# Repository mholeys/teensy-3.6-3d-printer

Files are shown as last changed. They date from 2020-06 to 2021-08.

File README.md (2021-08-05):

# Teensy 3.6 3D printer

KiCad board of my 3D printer

Uses a Teensy 3.6 - https://www.pjrc.com/store/teensy36.html
This requires most pins (including pins on the bottom of the teensy, as such I have left space for a row of wires to be soldered from the bottom of the teensy to the board.
This board was designed to replace a Anet A8 board so not all 3D printer features have been planned or taken into account.

Disclaimer:
- I am not a electrical engineer or certified in anyway for work with electronics, I am happy to take the risk myself but if you use this design you take all responsability, for any damage and you accept this.

Problems:
- After having the boards produced, I noticed that I have made a mistake with the holes for the custom boards such as the the rear pin breakout, and the TMC2130 driver holes. This has not been a problem for me as I have some smaller round hole pin headers, which fit perfectly, but you may have to redesign or modify this board in order to use something different.
- After using the board for a while, I have noticed I have also undersized the traces! (BAD, same problem as the original Anet A8 baord). This can be fixed by adding additional cabling between the GND input and the stepper motors, and importantly the transistors for the hot ends. This may make this board dangerous to use, and another reason not to use this board AS IS. 

Uses:
- https://github.com/XenGi/teensy_library
- https://github.com/XenGi/teensy.pretty

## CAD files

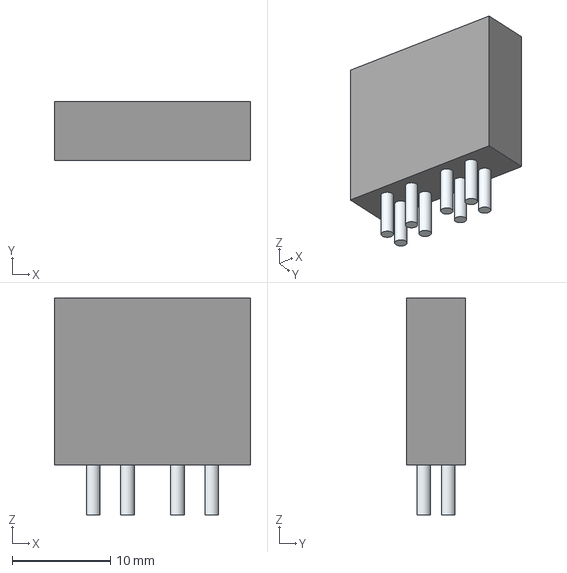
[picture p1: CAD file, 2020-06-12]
fuse/Pudenz-30a-PCB-ATO-Fuseholder.stp
20.0 x 6.00 x 22.1 mm
Leads x 9

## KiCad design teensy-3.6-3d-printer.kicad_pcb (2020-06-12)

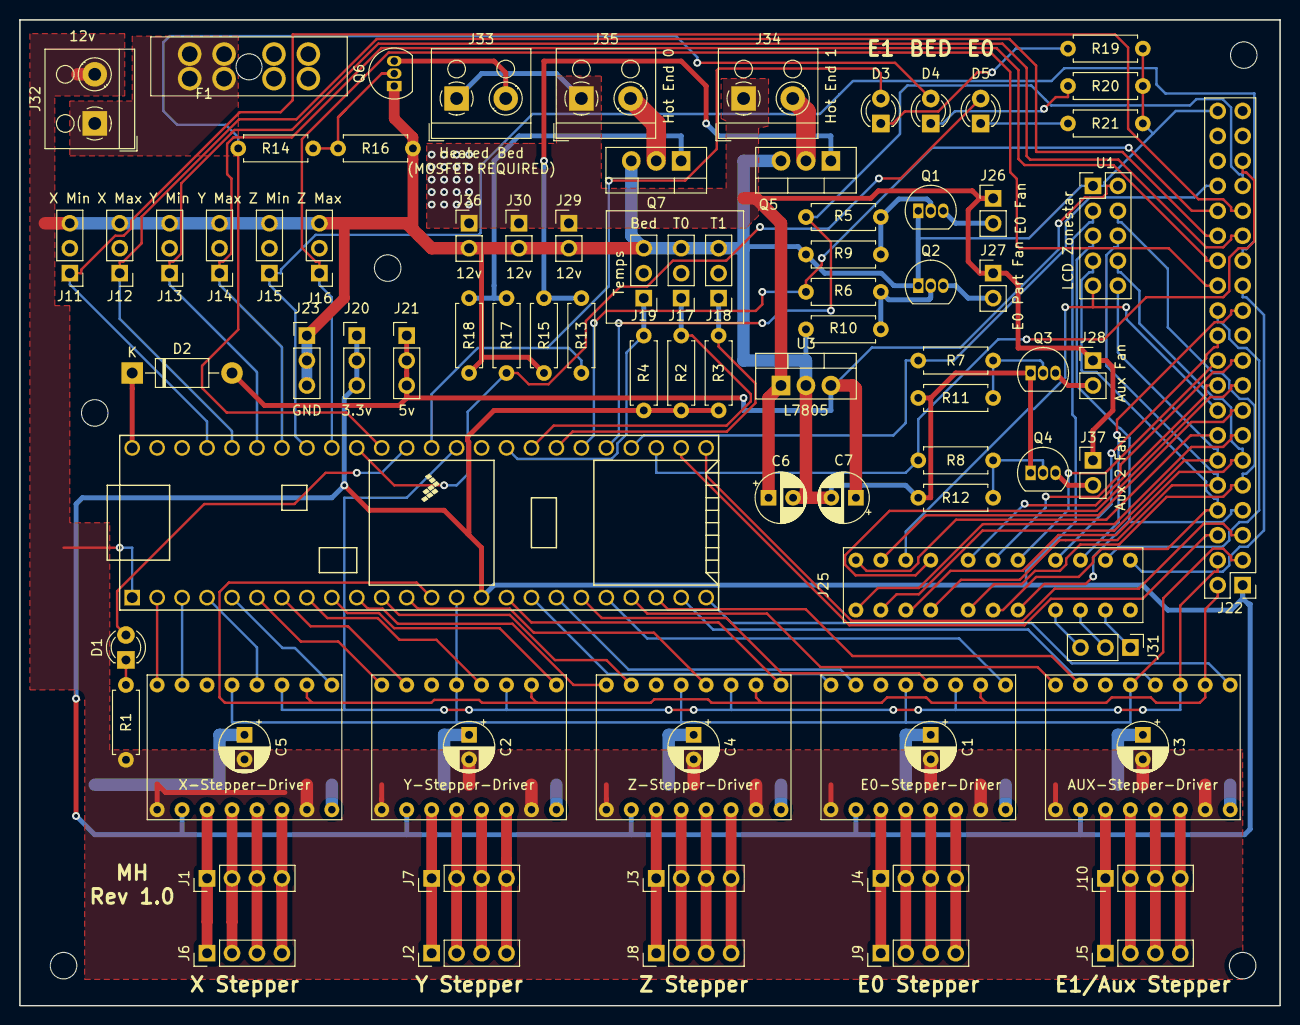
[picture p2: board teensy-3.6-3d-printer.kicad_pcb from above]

Board: 2 copper layers, 128.3 x 100.3 mm, 85 parts (0 on the bottom side), 107 nets.

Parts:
AUX-Stepper-Driver: TMC2130-Board; tmc2130-driver
C1, C2, C3, C4, C5: 100uf; CP_Radial_D5.0mm_P2.50mm
C6: 0.33uf; CP_Radial_D5.0mm_P2.50mm
C7: 0.1uf; CP_Radial_D5.0mm_P2.50mm
D1, D3, D4, D5: LED; LED_D3.0mm
D2: DIODE_SCHOTTKY_15V_1A; D_DO-41_SOD81_P10.16mm_Horizontal
E0-Stepper-Driver: TMC2130-Board; tmc2130-driver
F1: Fuse; Pudenz-30a-PCB-ATO-Fuseholder
J1, J6: X_STEPPER; PinHeader_1x04_P2.54mm_Vertical
J2, J7: Y_STEPPER; PinHeader_1x04_P2.54mm_Vertical
J3, J8: Z_STEPPER; PinHeader_1x04_P2.54mm_Vertical
J4, J9: E0_STEPPER; PinHeader_1x04_P2.54mm_Vertical
J5, J10: AUX_STEPPER; PinHeader_1x04_P2.54mm_Vertical
J11: X-Min-Limit; PinHeader_1x03_P2.54mm_Vertical
J12: X-Max-Limit; PinHeader_1x03_P2.54mm_Vertical
J13: Y-Min-Limit; PinHeader_1x03_P2.54mm_Vertical
J14: Y-Max-Limit; PinHeader_1x03_P2.54mm_Vertical
J15: Z-Min-Limit; PinHeader_1x03_P2.54mm_Vertical
J16: Z-Max-Limit; PinHeader_1x03_P2.54mm_Vertical
J17: Temp0; PinHeader_1x03_P2.54mm_Vertical
J18: Temp1; PinHeader_1x03_P2.54mm_Vertical
J19: Bed-Temp; PinHeader_1x03_P2.54mm_Vertical
J20: 3.3V; PinHeader_1x03_P2.54mm_Vertical
J21: 5V; PinHeader_1x03_P2.54mm_Vertical
J22: Conn_02x20_Counter_Clockwise; PinHeader_2x20_P2.54mm_Vertical
J23: GND; PinHeader_1x03_P2.54mm_Vertical
J25: teensy_back_pins; teensy-back
J26: Extruder 0 Fan; PinHeader_1x02_P2.54mm_Vertical
J27: Extruder 0 Part Fan; PinHeader_1x02_P2.54mm_Vertical
J28: Aux Fan; PinHeader_1x02_P2.54mm_Vertical
J29, J30, J36: 12V; PinHeader_1x02_P2.54mm_Vertical
J31: Debug; PinHeader_1x03_P2.54mm_Vertical
J32: Printer Power IN; TerminalBlock_RND_205-00001_1x02_P5.00mm_Horizontal
J33: Heated Bed; TerminalBlock_RND_205-00001_1x02_P5.00mm_Horizontal
J34: Hot End 1; TerminalBlock_RND_205-00001_1x02_P5.00mm_Horizontal
J35: Hot End 0; TerminalBlock_RND_205-00001_1x02_P5.00mm_Horizontal
J37: Aux 2 Fan; PinHeader_1x02_P2.54mm_Vertical
Q1, Q2, Q3, Q4, Q6: PN2222A; TO-92_Inline
Q5, Q7: IRLZ44N; TO-220-3_Vertical
R1, R14, R19, R20, R21: R; R_Axial_DIN0207_L6.3mm_D2.5mm_P7.62mm_Horizontal
R2, R3, R4: 4.7K; R_Axial_DIN0207_L6.3mm_D2.5mm_P7.62mm_Horizontal
R5, R6, R7, R8, R13, R17: 1K; R_Axial_DIN0207_L6.3mm_D2.5mm_P7.62mm_Horizontal
R9, R10, R11, R12, R15, R16, R18: 100K; R_Axial_DIN0207_L6.3mm_D2.5mm_P7.62mm_Horizontal
U1: Zonestar-LCD2004; PinHeader_2x05_P2.54mm_Vertical
U2: Teensy3.6; Teensy35_36
U3: L7805; TO-220-3_Vertical
X-Stepper-Driver: TMC2130-Board; tmc2130-driver
Y-Stepper-Driver: TMC2130-Board; tmc2130-driver
Z-Stepper-Driver: TMC2130-Board; tmc2130-driver

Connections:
+3V3: AUX-Stepper-Driver.3, E0-Stepper-Driver.3, J20.1, J20.2, J20.3, J22.1, R2.1, R3.1, R4.1, U1.3, U2.15, X-Stepper-Driver.3, Y-Stepper-Driver.3, Z-Stepper-Driver.3
+5V: C7.1, D2.2, J21.1, J21.2, J21.3, U1.2, U3.3
+12V: AUX-Stepper-Driver.15, C1.1, C2.1, C3.1, C4.1, C5.1, C6.1, E0-Stepper-Driver.15, F1.1, J26.1, J27.1, J28.1, J29.1, J30.1, J33.1, J34.1, J35.1, J36.1, J37.1, U3.1, X-Stepper-Driver.15, Y-Stepper-Driver.15, Z-Stepper-Driver.15
AUX2_FAN: J22.35, R8.2, U2.32
AUX2_FAN_12V: J37.2, Q4.3
AUX_CS: AUX-Stepper-Driver.10, U2.23
AUX_DIR: AUX-Stepper-Driver.2, U2.21
AUX_ENABLE: AUX-Stepper-Driver.16, U2.24
AUX_FAN: J22.34, R7.2, U2.33
AUX_FAN_12V: J28.2, Q3.3
AUX_RX: J22.5, U2.30
AUX_STEP: AUX-Stepper-Driver.4, U2.22
AUX_TX: J22.6, U2.31
BACK_46: J22.13, J25.46
BACK_47: J22.14, J25.47
BACK_48: J22.15, J25.48
BACK_50: J22.17, J25.50
BACK_51: J22.18, J25.51
BACK_52: J22.19, J25.52
BACK_53: J22.20, J25.53
BACK_54: J22.22, J25.54
BACK_55: J22.23, J25.55
BACK_56: J22.24, J25.56
BACK_57: J22.25, J25.57
BED_HEATER_12V: J33.2, Q6.3
E0_CS: E0-Stepper-Driver.10, U2.19
E0_DIR: E0-Stepper-Driver.2, U2.17
E0_ENABLE: E0-Stepper-Driver.16, U2.20
E0_FAN: J22.33, R5.2, U2.34
E0_FAN_12V: J26.2, Q1.3
E0_HEATER_12V: J35.2, Q7.2
E0_PART_FAN: J22.32, R6.2, U2.35
E0_PART_FAN_12V: J27.2, Q2.3
E0_STEP: E0-Stepper-Driver.4, U2.18
E1_HEATER_12V: J34.2, Q5.2
GND: AUX-Stepper-Driver.1, AUX-Stepper-Driver.13, C1.2, C2.2, C3.2, C4.2, C5.2, C6.2, C7.2, E0-Stepper-Driver.1, E0-Stepper-Driver.13, J11.3, J12.3, J13.3, J14.3, J15.3, J16.3, J17.3, J18.3, J19.3, J22.40, J23.1, J23.2, J23.3, J29.2, J30.2, J32.2, J36.2, Q1.1, Q2.1, Q3.1, Q4.1, Q5.3, Q6.1, Q7.3, R1.1, R9.1, R10.1, R11.1, R12.1, R15.2, R16.1, R18.2, R19.1, R20.1, R21.1, U1.1, U2.1, U3.2, X-Stepper-Driver.1, X-Stepper-Driver.13, Y-Stepper-Driver.1, Y-Stepper-Driver.13, Z-Stepper-Driver.1, Z-Stepper-Driver.13
HEATER_BED: D4.2, R14.2, U2.43
HEATER_E0: D5.2, R17.2, U2.44
HEATER_E1: D3.2, R13.2, U2.41
LCD_ADC_KEYPAD: J22.16, J25.49, U1.9
LCD_D4: J22.9, J25.42, U1.4
LCD_D5: J22.10, J25.43, U1.6
LCD_D6: J22.11, J25.44, U1.8
LCD_D7: J22.12, J25.45, U1.10
LCD_ENABLE: J22.8, J25.41, U1.7
LCD_RESET: J22.7, J25.40, U1.5
MISO: AUX-Stepper-Driver.8, E0-Stepper-Driver.8, J22.3, U2.14, X-Stepper-Driver.8, Y-Stepper-Driver.8, Z-Stepper-Driver.8
MOSI: AUX-Stepper-Driver.14, E0-Stepper-Driver.14, J22.2, U2.13, X-Stepper-Driver.14, Y-Stepper-Driver.14, Z-Stepper-Driver.14
unnamed: AUX-Stepper-Driver.5, J5.1, J10.1
unnamed: AUX-Stepper-Driver.7, J5.2, J10.2
unnamed: AUX-Stepper-Driver.9, J5.3, J10.3
unnamed: AUX-Stepper-Driver.11, J5.4, J10.4
unnamed: D1.1, R1.2
unnamed: D2.1, U2.53
unnamed: D3.1, R19.2
unnamed: D4.1, R20.2
unnamed: D5.1, R21.2
unnamed: E0-Stepper-Driver.5, J4.1, J9.1
unnamed: E0-Stepper-Driver.7, J4.2, J9.2
unnamed: E0-Stepper-Driver.9, J4.3, J9.3
unnamed: E0-Stepper-Driver.11, J4.4, J9.4
unnamed: F1.2, J32.1
unnamed: J1.1, J6.1, X-Stepper-Driver.5
unnamed: J1.2, J6.2, X-Stepper-Driver.7
unnamed: J1.3, J6.3, X-Stepper-Driver.9
unnamed: J1.4, J6.4, X-Stepper-Driver.11
unnamed: J2.1, J7.1, Y-Stepper-Driver.5
unnamed: J2.2, J7.2, Y-Stepper-Driver.7
unnamed: J2.3, J7.3, Y-Stepper-Driver.9
unnamed: J2.4, J7.4, Y-Stepper-Driver.11
unnamed: J3.1, J8.1, Z-Stepper-Driver.5
unnamed: J3.2, J8.2, Z-Stepper-Driver.7
unnamed: J3.3, J8.3, Z-Stepper-Driver.9
unnamed: J3.4, J8.4, Z-Stepper-Driver.11
unnamed: J25.DC, J31.2
unnamed: J25.DD, J31.3
unnamed: J25.DE, J31.1
unnamed: Q1.2, R5.1, R9.2
unnamed: Q2.2, R6.1, R10.2
unnamed: Q3.2, R7.1, R11.2
unnamed: Q4.2, R8.1, R12.2
unnamed: Q5.1, R13.1, R15.1
unnamed: Q6.2, R14.1, R16.2
unnamed: Q7.1, R17.1, R18.1
SCK: AUX-Stepper-Driver.12, E0-Stepper-Driver.12, J22.4, U2.40, X-Stepper-Driver.12, Y-Stepper-Driver.12, Z-Stepper-Driver.12
STATUS_LED: D1.2, U2.42
TEMP_BED: J19.1, R4.2, U2.38
TEMP_E0: J17.1, R2.2, U2.37
TEMP_E1: J18.1, R3.2, U2.36
X_CS: U2.4, X-Stepper-Driver.10
X_DIR: U2.2, X-Stepper-Driver.2
X_ENABLE: U2.5, X-Stepper-Driver.16
X_MAX: J12.1, J22.30, U2.49
X_MIN: J11.1, J22.31, U2.50
X_STEP: U2.3, X-Stepper-Driver.4
Y_CS: U2.8, Y-Stepper-Driver.10
Y_DIR: U2.6, Y-Stepper-Driver.2
Y_ENABLE: U2.9, Y-Stepper-Driver.16
Y_MAX: J14.1, J22.28, U2.47
Y_MIN: J13.1, J22.29, U2.48
Y_STEP: U2.7, Y-Stepper-Driver.4
Z_CS: U2.12, Z-Stepper-Driver.10
Z_DIR: U2.10, Z-Stepper-Driver.2
Z_ENABLE: U2.16, Z-Stepper-Driver.16
Z_MAX: J16.1, J22.26, U2.45
Z_MIN: J15.1, J22.27, U2.46
Z_STEP: U2.11, Z-Stepper-Driver.4

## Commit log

2019-12-10 Started teensy-3.6 schematic
    [teensy-3.6-3d-printer.kicad_pcb, teensy-3.6-3d-printer.sch]
2019-12-11 Teensy schematic finished
    [teensy-3.6-3d-printer.sch]
2020-01-08 Revision 1 finished
    [teensy-3.6-3d-printer.kicad_pcb, teensy-3.6-3d-printer.sch]
2020-06-12 Changed to new fuse holder, added filled zones
    [Pudenz-30a-PCB-ATO-Fuseholder.stp, teensy-3.6-3d-printer.kicad_pcb, teensy-3.6-3d-printer.sch]
